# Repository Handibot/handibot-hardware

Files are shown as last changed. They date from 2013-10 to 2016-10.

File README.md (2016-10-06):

handibot-hardware
=================

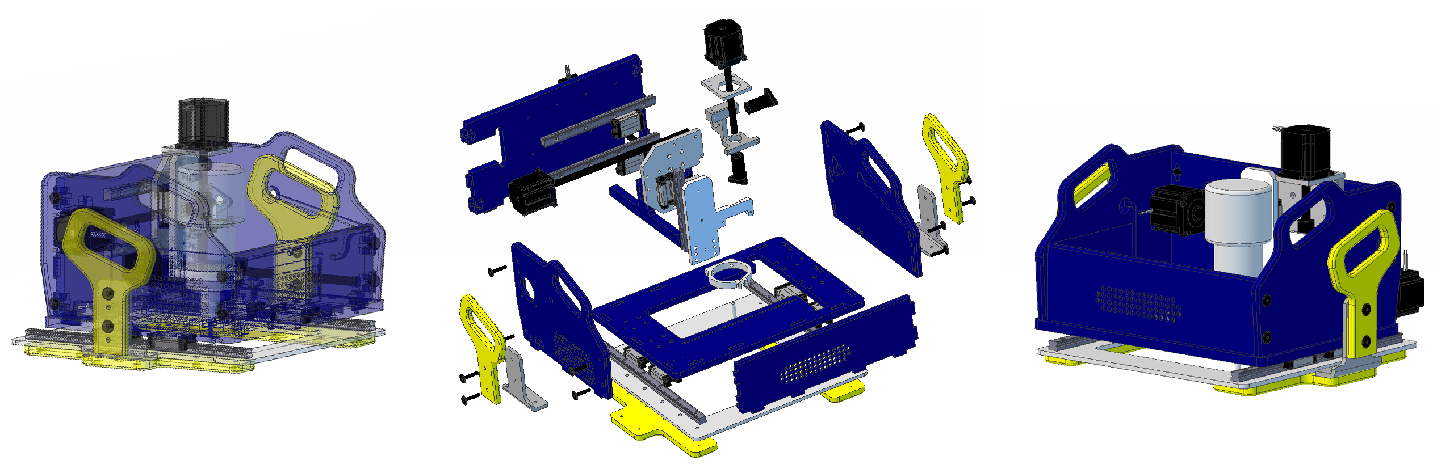
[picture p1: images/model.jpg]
Handibot Assembly


A Handibot tool is a new kind of portable, digitally-controlled power tool for cutting, drilling, carving, and many other machining operations– the first Universal Digital Power Tool (UDPT) – or just, a Smart Tool. If you're familiar with industrial CNC (computer numerically controlled) equipment, think of the Handibot tool as a portable version of CNC. But instead of taking material to a stationary machine, you bring the Handibot to your material -- your jobsite, your remodeling task, your project, your work.

You can put your Handibot tool to work on a table, the floor, the ceiling, the wall, wherever you need to precisely cut, drill, or carve. Armed with a software application developed just for the kind of job you need to do, a Handibot tool is ready to go to work on your job, task, or project with a squeeze of the “Start” button.

Open Source
===========
Handibot is an “open innovation” project. Handibot runs on the open-source, [FabMo digital fabrication platform](https://gofabmo.org). And, to encourage the evolution of hardware and accessories, Handibots are open source hardware (OSH or OSHW). This GitHub repository is the definitive open source hardware documentation for the Handibot system.

The philosophy of this open-source project and our plans for its development can be found on the [Handibot website Open-Innovation pages](https://handibot.com/open-source.php#open_innovation). We recognize that hardware sources and documentation placed on GitHub, while properly archival, can be difficult to view. So as a supplement, we additionally place the definitive STP files as well as additional production files and documents on more exploration-friendly sites which we strive to keep current.

At the moment, Handibot materials can be explored on [GrabCAD](https://workbench.grabcad.com/workbench/projects/gcuAc_g79JwJj5xoyB_sCtAKoUyXaXH0NyeRYptWOwEOWN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). 

For more Handibot Information and our Kickstarter history, see these links:

* [Handibot Website](http://www.handibot.com)
* [Handibot Kickstarter](http://www.kickstarter.com/projects/1320575205/handibottm-a-smart-digital-power-tool?ref=live)

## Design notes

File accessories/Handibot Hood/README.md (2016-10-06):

Handibot Hood
=============

![Handibot Hood]
(https://github.com/Handibot/handibot-hardware/blob/master/accessories/Handibot%20Hood/Handibot_Hood.png)

An eclosure for Handibot v1.0 and v1.1. This "Hood" helps contain dust and debris and reduces router noise. Designed by David Preiss.

* STP Model of parts for full Enclosure (Hood 1.0)

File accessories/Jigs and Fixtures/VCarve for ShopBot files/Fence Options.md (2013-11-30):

# Handibot Fence options #

Two options for a fixed front fence for a Handibot Smart Power Tool. The edge of the fences line up with the Y=0 point of the tool when zeroed with the homing switches, which gives an accurate reference point for cutting.

Two options are shown for a replaceable sacrificial section in the section where cutting happens..a press-fit insert that is cut with the Handibot, and a 1/4"  thick insert that is attached with double-sided carpet tape.

The parts are cut with a 1/4" diameter bit and the file has two layers. The *t-nut pocket* layer contains shallow recesses for the two t-nuts and should be run first. The *cutout* layer drills holes and cuts out the fence.

After the cutting is complete, press or hammer two t-nuts into the recess in the bottom, then flip the fence over and bolt it to the front edge of the Handibot using the two bolt holes in the yellow base.

**NOTE:** *The right-most flange of the clear acrylic base lines up with the right-most bolt hole in the front of the yellow base, and even though the heads of the bolts are low profile there is a chance that the flange may hit the bolt head. If that looks like it's going to happen on your tool, the front edge of that flange can be filed or ground a little to give clearance.*

## Materials ##

- 3/4" plywood, HDPE, mdf, or similar stable sheet goods, at least 20" x 2.5". File is sized for material that is actually .72" thick which seems to most common. Also 1/4" thick material if the thin insert is used, 6.5" long x .72" wide 

- 2 @ 1/4-20 4-prong t-nut... [http://shop.stafast.com/t-nuts/standard/4-prong/142074](http://shop.stafast.com/t-nuts/standard/4-prong/142074) or equivalent

- 2@ 1/4-20 x 25mm decorative bolts... [http://shop.stafast.com/bolts/decorative-head-bolts/17mm-head-no-shoulder/bb142025uhdft](http://shop.stafast.com/bolts/decorative-head-bolts/17mm-head-no-shoulder/bb142025uhdft) or equivalent

- a 4mm or 5/32" Allen wrench

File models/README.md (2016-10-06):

Handibot Base Model (STP) History
=================================
(We have selected STP files to provide the definitive versions of Handibot. Along with PDF BOM's in a separate folder, they consititute the reference design for Handibots and are stored here on GitHub. We will make other types of models, documentation, and production files available as appropriate and convenient. These we will strive to keep updated and available at sites that make exploration convenient.)

* Initial Handibot V 1.00.00 (Publically shown at launch at HIW and Marker Faire, San Mateo, May 2013; earlier prototypes from 7/2012)
* Handibot V 1.01.00 (from 9/10/2013; first Kickstarter Production version)
* Handibot V 1.02.00 (1/13/2014; includes small updates to Kickstarter)
* Handibot V 1.03.00 (3/12/2014; Release Version "Handibot Developer Edition")
* Handibot V 1.10.00 (1/15/2015; Updated "1.1 Developer Edition")
* Handibot V 1.10.07 (9/18/2015; last release of "Developer Edition")

* Handibot V 2.00.00 (3/1/2016; Release Version "Handibot Adventure Edition")

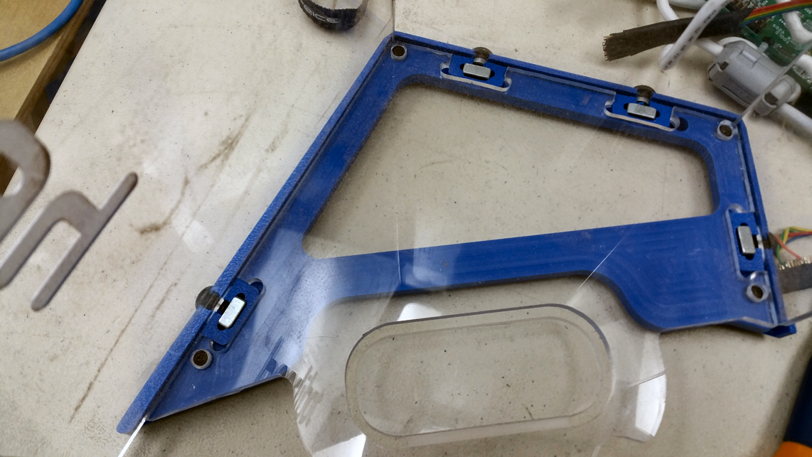
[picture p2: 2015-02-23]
accessories/Handibot Hood/Hood_EndPiece_Inside.png

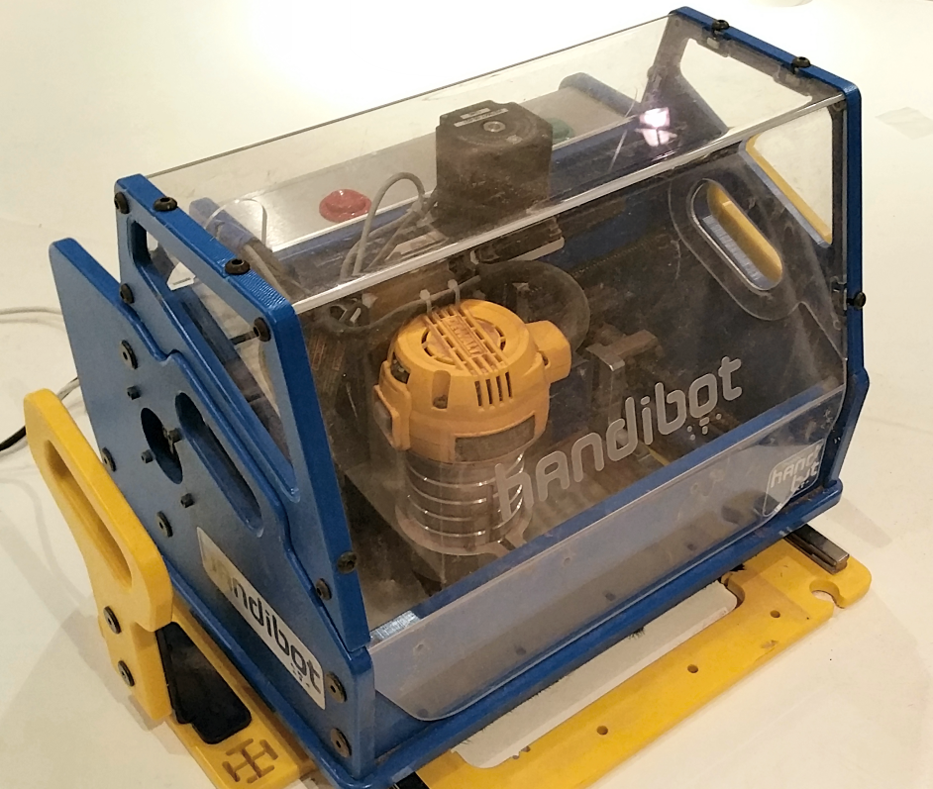
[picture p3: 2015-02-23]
accessories/Handibot Hood/Handibot_Hood.png

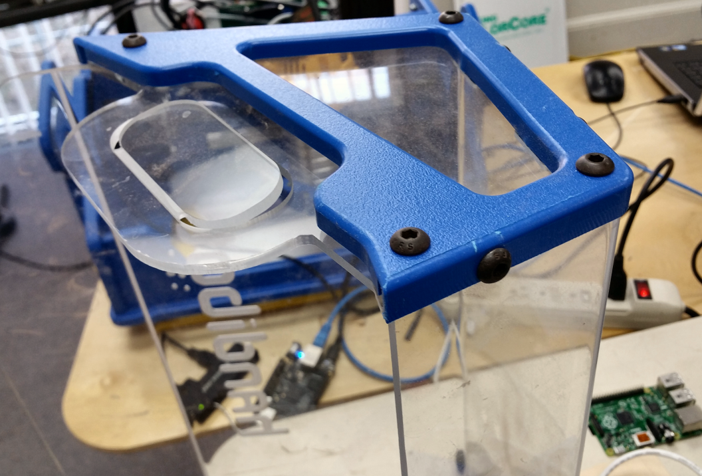
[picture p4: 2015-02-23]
accessories/Handibot Hood/Hood_EndPiece_Outside.png

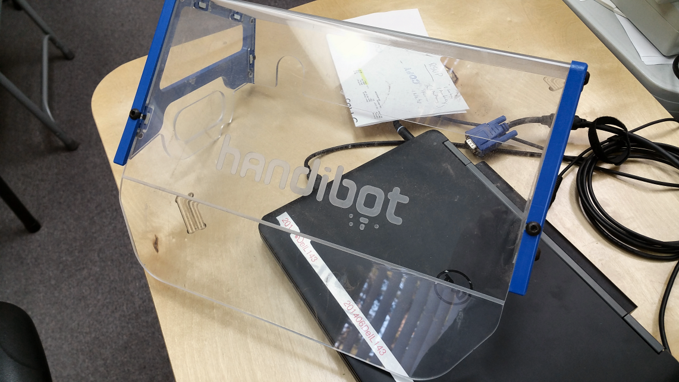
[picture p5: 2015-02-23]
accessories/Handibot Hood/Hood_Acrylic_Front.png

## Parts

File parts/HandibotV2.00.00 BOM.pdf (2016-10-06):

Handibot V2.0

Description | Vendor | Vendor # | SB part # | Qty
Total Sales Price | | | | 1
Assembly Labor | | | | 8
X Gusset | USAD | 4762 | 2
Nut Bracket | USAD | 4761 | 2
Z Plate | USAD | 4652 | 1
Router Bracket Connector | USAD | 4654 | 1
Router Bracket Upper | USAD | 4655 | 1
Router Bracket Lower | USAD | 4656 | 1
Z Motor Plate | USAD | 4657 | 1
X-Z Carriage | USAD | 4659 | 1
X Rail Backing Plate | USAD | 4660 | 1
X Motor Plate | USAD | 4661 | 1
Y Bearing Backing Plate | USAD | 4662 | 2
Y Nut Holder | USAD | 004894 | 1
Cable Guide Tray | USAD | 4663 | 1
Cable Guide Barrier | USAD | 4664 | 1
Z Zero Plate | USAD | 4665 | 1
Y Motor Plate | USAD | 4666 | 1
Base Plate Backing | USAD | 4667 | 1
Y Nut Bracket | USAD | 4668 | 1
Bracket Universal Mount | USAD | 3653 | 2
Handibot Machined Parts Kit | USAD | 4764 | 1
Hood Face | Handibot | 4669 | 1
Hood Side Window | Handibot | 4670 | 2
Electronics Enclosure | Handibot | 4671 | 1
LED Strip Cover | Handibot | 4672 | 1
Tool Holder Window | Handibot | 4673 | 1
Rear Neoprene Plate | Handibot | 4674 | 1
Front Neoprene Plate | Handibot | 4675 | 1
Side Neoprene Plate | Handibot | 4676 | 1
Rear Neoprene | Handibot | 4677 | 1
Front Neoprene | Handibot | 4678 | 1
Side Neoprene | Handibot | 4679 | 1
Logo Plate | Handibot | 4680 | 2
Base Plate HDPE | Handibot | 4681 | 1
Button Holder HDPE | Handibot | 4682 | 1
Electronics Partition HDPE | Handibot | 4683 | 1
Electronics Wall HDPE | Handibot | 4684 | 1
Tool Holder Frame HDPE | Handibot | 4685 | 1
Vacuum Foot HDPE | Handibot | 4686 | 1
Rear Wall HDPE | Handibot | 4687 | 1

## Bill of Materials

Hood Left Side HDPE | Handibot | | 4688 | 1
Hood Right Side HDPE | Handibot | | 4689 | 1
Tie Plate HDPE | Handibot | | 4690 | 1
Y Motor Holder HDPE | Handibot | | 4691 | 1
Mid Plate HDPE | Handibot | | 4692 | 1
Y Motor Guard HDPE | Handibot | | 4693 | 1
ExoFrame Base HDPE | Handibot | | 4694 | 1
Sensor Holder HDPE | Handibot | | 4695 | 0
ExoFrame Left Side HDPE | Handibot | | 4696 | 1
ExoFrame Right Side HDPE | Handibot | | 4697 | 1
Handle HDPE | Handibot | | 4704 | 1
Handibot Cut Parts Kit | Handibot | | 4765 | 1
Motor Actuator X 315mm | Haydon Kerk | K57M4Y-05-019 | 3621 | 1
Motor Actuator Y 270mm | Haydon Kerk | K57M4Y-05-020 | 3622 | 1
Motor Actuator Z 150mm | Haydon Kerk | K57M4Y-05-021 | 3623 | 1
Block Linear Rail | Accu-Tech | SME 15SBSSFC | 3864 | 7
Assembly Rail Linear 242 | Accu-Tech | SME 15 SB 1 SS +R242-31/31N | 4093 | 2
Rail Linear 366 | Accu-Tech | SME 15 SB 2 SS +T366 -33/33N | 4076 | 2
Assembly Rail Linear 168 | Accu-Tech | SME 15 SB 1 SS +R168 -24/24N | 4095 | 1
Micro Step Drive G250X | Gecko Drive | G250X | 2780 | 4
Assy Interface Handibot | GRT | HB-5 | 4544 | 1
Fabmo Card | | | 4629 | 1
Power Supply | Emco | HRP-150-24 | 3664 | 1
Switch Stop | Spark Fun | COM-09336 | 3662 | 1
Switch Go | Spark Fun | COM-09341 | 3663 | 1
Cord Power | Jameco | 2099999 | 3711 | 1
Guard Fan | Jameco | 1952708 | 3713 | 1
Board Arduino | Spark Fun | DEV-11113 | 3697 | 1
Lights Indicator LED | AdaFruit | 001138 | 3698 | 0.16
Thermal Pad 0.10x8x16 | Digikey | 926-1114-ND | 3118 | 0.166
WAGO right angle | EMCO | | | 1
Connector Wago 2 Pin Male | EMCO | 231-602 | 163 | 1
WAGO Board Connector | EMCO | | 004177 | 2
Switch Rocker W/V Lock | Digikey | 486-1638-ND | 3834 | 1
Cable 18 2C Unshielded | Machine Controls | 450003-15 | 4705 | 52
Cable 4C 18 AWG STR BC | ANIXTER | 8489 | 95 | 34
Cable 2Cx0.25 Br & W | Machine Controls | 117039 | 3004 | 12
Black 18 AWG | Digikey | C2064B-1000-ND | 4600 | 20
White 18 AWG | Digikey | C2064W-1000-ND | 159 | 19
Blue 18 AWG | Digikey | C2064L-1000-ND | 4838 | 14
Green 18 AWG | Digikey | C2064G-1000-ND | 4601 | 5
Ribbon Cable | Jameco | 643559 | 864 | 6
USB Short cable | | | | 1
Heat Shrink 2"x40mm Black | Heat Shrink | B2(3x)x40mm | 1648 | 1.5
22-16 AWG Female Disconnect | Jameco | 489627 | 3796 | 8
Grey Ferrule | Fastenal | 0749603 | 3419 | 2

White Ferrule | Fastenal | 0749600 | 3505 | 4
Red Ferrule | Fastenal | 0749607 | 3777 | 1
18-22 AWG Female Terminal | Jameco | 489643 | 3795 | 4
Z Zero Clip | Digikey | 314-1084-ND | 4790 | 1
Relay 24V | Digikey | PB1008-ND | 3699 | 1
Connector Fork 22-16 AWG | Fastenal | 0720185 | 2758 | 11
Zip Tie Anchor | McMaster | 7566K29 | 4821 | 3
Cable Tie 6" Black | Fastenal | 63124 | 3108 | 13
M3x16 BHSCS | McMaster | 92095A184 | 5079 | 2
M4x10 SHCS | Fastenal | 39524 | 3053 | 10
M4x16 SHCS | McMaster | 90128A215 | 4818 | 14
M4x20 SHCS | Fastenal | 11103313 | 3096 | 6
M4x14 BHSCS | Fastenal | 39901 | 4748 | 17
M4x16 BHSCS | Fastenal | 39902 | 4749 | 19
M4x20 BHSCS | Fastenal | 39903 | 4750 | 1
M4 x 10 FHSCS | McMaster | 91294A190 | 4822 | 2
M4 x 10 Nylon Screw | McMaster | 92492A220 | 4816 | 2
M5 x 20 SHCS | Fastenal | | 3873 | 2
M5x10 BHSCS | Fastenal | MB2540010A2000 | 4751 | 8
M5x14 BHSCS | Fastenal | 11510097 | 3810 | 12
M5x20 FHSCS | Fastenal | 1139947 | 4753 | 4
M6x18 FHSCS | Fastenal | 40947 | 4755 | 5
2-56x1/4 SHCS | Fastenal | 73399 | 4743 | 8
6-32 x 5/16 BHSCS | Fastenal | 73763 | 4744 | 8
6-32 x 5/8 Standoff | Fastenal | 146059 | 4759 | 4
1/4-20 x 1/2 BHSCS | Fastenal | 24049 | 2134 | 11
1/4-20 x 3/4 BHSCS | Fastenal | 24051 | 2135 | 1
1/4-20 x 1 BHSCS | Fastenal | 140675 | 3802 | 7
1/4-20 x 7/16 FHSCS | McMaster | 92210A536 | 4817 | 1
1/4-20 x 20mm Connector Bolt | Fastenal | 140675 | 3802 | 4
1/4-20 x 30mm Connector Bolt | Fastenal | 140679 | 3667 | 37
1/4-20 Square Nut | Fastenal | 37619 | 4419 | 48
#6 x 3/8 FH Sheet Metal Screw | Fastenal | 31528 | 4756 | 6

#6x1/2 PPH | Fastenal | 1131226 | 4423 | 2

#8 x 3/8 PPH | Fastenal | 0143200 | 4422 | 8

#8 x 3/8 FH Sheet Metal Screw | Fastenal | 148505 | 4757 | 25

#8x1/2 Pan Head | Fastenal | 0143318 | 4421 | 2

#10 x 1/2 Pan Head | Fastenal | 31341 | 4758 | 9

1/4x1/4x#8 Aluminum Spacer | Fastenal | 146031 | 4760 | 2
Plastic Countersunk Washer | McMaster | 95481A035 | 4819 | 1
0.375 x 0.25 Magnet | Apex Mag | M38x14DI | 4815 | 4
Vacuum Tube | McMaster | 5500K31 | 4789 | 1.2
Brush 120"x1.6" Exposed | Sealeze | FXD80IH16BL | 3376 | 12.5
Extension Spring | McMaster
3/8 x 0.012 Spring Steel Banding | McMaster | 9075K46 | 4820 | 13
3mm T Handle Allen | McMaster | | 005080 | 1

4mm T Handle Allen | McMaster | 4787

1
2mm Allen L key | | | 005081 | 1
Pointer | Handibot | | 4788
User Manual | Handibot | | 4786 | 1
vCarve Pro | Vectric | | 11149
ShopBot Control License | ShopBot | | 11161 | 1
Dewalt Router | Dewalt | | 12012
Foam Back Packaging | Handibot | | 4768 | 2
Foam Bottom Packaging | Handibot | | 4769
Foam Top Packaging | Handibot | | 4770 | 1
Foam Front Packaging | Handibot | | 4771
Test Board | Handibot | | | 1
Box 22 x 18 x 16 | Uline | S-16458 | 4767

1

1

1

1

1

1

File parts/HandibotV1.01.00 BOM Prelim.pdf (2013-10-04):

Part # | PART NAME | REQUIRED
003646-01 | Exoframe Side Right HDPE | 1
003647-01 | Exoframe Side Left HDPE | 1
003648-01 | Exoframe Front HDPE | 1
003649-01 | Exoframe Rear HDPE | 1
003650-01 | Exoframe Bottom HDPE | 1
003674-01 | Pad Base HDPE | 1
003652-01 | Handle Outboard HDPE | 2
003653-01 | Bracket Universal Mount | 2
| Cover Fairing Acrylic
| Linear Motion
003621-01 | Motor Actuator X 315mm | 1
003622-01 | Motor Actuator Y 270mm | 1
003623-01 | Motor Actuaror Z 150mm | 1
with motor | Nut Antibacklash X | 1
with motor | Nut Antibacklash Y | 1
with motor | Nut Antibacklash Z | 1
003655-01 | Carrier Antibacklash nut Y HDPE | 1
002876-01 | Carrier Antibacklash nut Z&X Aluminum | 2
003656-01 | Rail Anti Backlash Nut Carrier Y HDPE | 1
004002-01 | Rail Linear X 235mm | 2
004003-01 | Rail Linear Y 360mm | 2
004004-01 | Rail Linear Z 162mm | 1
004001-01 | Bearing Linear Rail X,Y,Z | 7

Carriage
003657-01 | Plate Carriage | 1
003658-01 | Plate Z | 1
003659-01 | Plate Motor Z | 1

003660-01 | Bracket Router | 1
003661-01 | Gusset Z Plate | 1
| Electronics
002780-01 | Driver Gecko X,Y,Z | 3
003118-01 | Thermal Pad heatsink plate | 1
003591-01 | Board Interface | 1
003601-01 | Card Controller | 1
003662-01 | Switch Stop | 1
003663-01 | Switch Go | 1
| Board Arduino | 1
| Lights Indicator LED | 1
003664-01 | Power Supply 24V 150W | 1
| Contactor 24V | 1
003665-01 | Switch Rocker | 1

Wire
Crimp connectors
Heat shrink

Hardware
T-nut dropin | 27
Bolt 1/4" x30mm | 27
Standoff Interface board | 4
SHCS M4x12 | 32
SHCS M4x16 | 15
SHCS M4x20 | 4
BHCS M5x20 | 2
SHCS M6x20 | 28
Nut nylock M4 | 8
BHCS M4x40 | 3
SHCS M4x70 | 4
bolts for standoffs/heatsink plate | 8
SHCS #2-56 | 6
Router Dewalt | 1

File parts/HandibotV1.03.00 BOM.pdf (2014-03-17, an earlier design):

Vendor Part # | SB Part # | Vendor of Record | Category | QTY. REQ
| | | Mechanical
| 003651 | Norva Plastics | HDPE BLUE 4x10x.5 (Compression Polymers) | 0.2500
| 003677 | Norva Plastics | HDPE YELLOW 4x10x.5 (Compression Polymers) | 0.08
003646 | 003646 | Norva Plastics/Shopbot | Exoframe Side Right HDPE | 1
003647 | 003647 | Norva Plastics/Shopbot | Exoframe Side Left HDPE | 1
003648 | 003648 | Norva Plastics/Shopbot | Exoframe Front HDPE | 1
003649 | 003649 | Norva Plastics/Shopbot | Exoframe Mid HDPE | 1
003650 | 003650 | Norva Plastics/Shopbot | Exoframe Bottom HDPE | 1
003674 | 003674 | Norva Plastics/Shopbot | Baseplate | 1
003652 | 003652 | Norva Plastics/Shopbot | Handle Outboard HDPE | 2
003676 | 003676 | Norva Plastics/Shopbot | Exoframe Lid Partition HDPE | 1
003675 | 003675 | Norva Plastics/Shopbot | Exoframe Partition Rt HDPE | 1
003671 | 003671 | Norva Plastics/Shopbot | Exoframe Partition Lt HDPE | 1
003670 | 003670 | Norva Plastics/Shopbot | Exoframe Rear HDPE | 1
003653 | 003653 | Norva Plastics/Shopbot | Bracket Universal Mount | 2
80664 | 003696 | Century Spring | Spring Z Assit | 1
| 003710 | Raleigh Rubber and Gasket | Neoprene 4x8x.0625" with Pressure sensitive adhesive applied | 0.0556
003703 | 003703 | Raleigh Rubber and Gasket/Shopbot | Pad Baseplate Neoprene | 1
003865 K57M4Y-05-019 | 003865 | Norva Plastics/Shopbot | Baseplate Pointer | 1
| | | Linear Motion
| 003621 | Haydon Kerk | Motor Actuator X 315mm | 1
K57M4Y-05-020 | 003622 | Haydon Kerk | Motor Actuator Y 270mm | 1
K57M4Y-05-021 | 003623 | Haydon Kerk | Motor Actuaror Z 150mm | 1
002876 | 002876 | USA Dutch | Nut Block Upper | 2
003655 | 003655 | USA Dutch | Carrier Antibacklash nut Y Aluminum | 1
003656 | 003656 | USA Dutch | Rail Anti Backlash Nut Carrier Y HDPE | 1
MSB 15 SS FCN | 004001 | Accu-Tech USA | Block | 7
MSB 15 T235-27.5/27.5 N | 004002 | Accu-Tech USA | Rail Linear X 235mm | 2
MSB 15 T360-30/30 N | 004003 | Accu-Tech USA | Rail Linear Y 350mm | 2
MSB 15 U162-21/21 N | 004004 | Accu-Tech USA | Rail Linear Z 162mm | 1
| | | Carriage
003311 | 003311 | USA Dutch | Mount Spring DT Z | 1
003657 | 003657 | USA Dutch | Plate Carriage | 1
003658 | 003658 | USA Dutch | Plate Z | 1
003659 | 003659 | USA Dutch | Plate Motor Z | 1
003660 | 003660 | USA Dutch | Bracket Router | 1
003661 | 003661 | USA Dutch | Gusset Z Plate | 1
003672 | | | Electronics
| 003672 | USA Dutch | Enclosure Electronics | 1
G250X | 002780 | Gecko Drive | MICRO STEP DRIVE G250X | 3
926-1114-ND | | Digikey | Thermal Pad .010" x 8" x 16" | 0.14
| 003118 | DigiKey/Shopbot | Thermal Pad heatsink plate | 1
| 003786 | GRT | Assy Interface Handibot | 1
| 003601 | PSI | Card Controller V211 | 1
USBPNLBFBM1 | 003685 | StarTech | Cable USB Panel Mount B to B - F/M 1 ft | 1
USBPRT | 002190 | Dramen | CABLE USB A/B | 1
COM-09336 | 003662 | Spark Fun | Switch Stop | 1
COM-09341 | 003663 | Spark Fun | Switch Go | 1
2099999 | 003711 | Jameco | Cord Power | 1

56P2967 | 003712 | Newark | Filter Fan Media | 1
1952708 | 003713 | Jameco | Guard Fan | 1
7378K225 | 003714 | McMaster-Carr | Loom Wire | 0.05
RP465-ND | 000102 | DigiKey | Cordgrip Power | 1
DEV-11113 | 003697 | Spark Fun | Board Arduino | 1
001138 | 003698 | AdaFruit | Lights Indicator LED | 0.16
HRP-150-24 | 003664 | Emco | Power Supply 24V 150W | 1
PB1008-ND | 003699 | DigiKey | Relay 24V | 1
WM2011-ND | 003128 | DigiKey | CONN HOUSING 2POS .100 W/RAMP | 3
WM1114CT-ND | 003129 | DigiKey | CONN TERM FEMALE 22-30AWG TIN | 6
CKN9956CT-ND | 003013 | DigiKey | SWITCH DETECT MICRO SPST SMD | 3
WM4200-ND | 003131 | DigiKey | CONN HEADER 2POS .100 VERT TIN | 3
473-1005-ND | 003132 | DigiKey | PCB COPPERCLAD 12X12 1/16" 1SIDE | 0.02
003700 | 003700 | ShopBot | Switch Proximity X | 1
003701 | 003701 | ShopBot | Switch Proximity Y | 1
003702 | 003702 | ShopBot | Switch Proximity Z | 1
1091-1162-ND | 003665 | DigiKey | Switch Rocker | 1
| | | Wire 18 AWG Black 20" | 0.00167
| | | Wire 18 AWG White 30" | 0.0025
410002-06 | 003694 | Machine Control | Wire 18 AWG Blue 30" | 0.0025
117039 | 003004 | Machine Control | Cable 2Cx0.25 Br & W 78" | 0.013
2003A | 001664 | Emco | Cable 3C BK R G 80 Deg. 300v 19" | 0.0016
643559 | 000864 | Jameco | Cable Ribbon 16C 6" | 0.005
117050 | 003008 | Machine Control | Cable DT MTR 4x0.34 31" | 0.00258
489643 | 003795 | Jameco | Quick Disconnect Terminal 18-22 AWG Female 19.81mm 8.02mm | 4
489627 | 003796 | Jameco | Quick Disconnect Terminal 18-22 AWG Female 21.84mm 9.65mm | 6
749600 | 003505 | Fastenal | 22 AWG 0.31"/7.8mm Strip Power Phase[REG] Wht Nylon Insulated Ferrule End Sleeve | 14
749603 | 003419 | Fastenal | 20 AWG 0.30"/7.5mm Strip Power Phase[REG] Gray Nylon Insulated Ferrule End Sleeve | 1
WM2901-ND | 003797 | DigiKey | Conn Housing 3 Pos Female .100 W/LATCH | 1
WM2513-ND | 003798 | DigiKey | Conn Term Female 24-30AWG GOLD | 3
WM2534-ND | 003799 | DigiKey | Conn Housing 3 Pos Male .100 | 1
WM2563CT-ND | 003800 | DigiKey | Conn Pin Male 24-30AWG CRIMP 15GOLD | 3
70078437 | 003801 | ALLIED | Ferrule, Dual Wire; 18 AWG; 2; HH 2 x 1.0/15; Red; 0.43 in.; 0.61 in.; 0.32 in. | 1
ASC16H-ND 961746 | 001535 | DigiKey | CONN IDC SOCKET 16POS | 2
| | | Hardware
| 003666 | Fastenal | T-nut dropin | 29
140679 | 003667 | Fastenal | Bolt Connector 1/4-20 x30mm | 29
140675 | 003802 | Fastenal | Bolt Connector 1/4-20 x20mm | 4
92492A128 | 003803 | McMaster-Carr | MS PPH M3x20 Nylon Black | 6
93369A116 | 003804 | McMaster-Carr | Nut hex Nylon Black | 6
1123201 | 001601 | Fastenal | SHCS 1/4-20 x 1/2 | 4
145924 | 003805 | Fastenal | Standoff 6-32 nylon | 4
1139524 | 003053 | Fastenal | SHCS M4x10 | 4
1139525 | 002910 | Fastenal | SHCS M4x12 | 41
1139518 | 003806 | Fastenal | SHCS M4x14 | 18
1139526 | 003396 | Fastenal | SHCS M4x16 | 5
1139527 | 003054 | Fastenal | SHCS M4x20 | 6
039536 | 003807 | Fastenal | SHCS M4x80 | 4
1139529 | 003668 | Fastenal | BHCS M4x30 | 2
1139545 | 003808 | Fastenal | SHCS M5x12 | 1

040878 | 003810 | Fastenal | BHCS M5x14 | 10
040879 | 003809 | Fastenal | BHCS M5x16 | 30
1140147 | 003562 | Fastenal | Nut hex nylock M4 | 12
1128795 | 003811 | Fastenal | MS PPH 6-32 x 3/8 | 4
90259A218 | 003812 | McMaster-Carr | Threaded insert M5 | 2
023024 | 002920 | Fastenal | SHCS #2-56 | 6
1139584 003746 | 003813 | Fastenal | SHCS M8-1.25x10 | 1
| | | Dust Collector | 1
| 003746 | Norva Plastics/Shopbot | Channel Dust Collector Front | 1
003747 | 003747 | Norva Plastics/Shopbot | Channel Dust Collector Rear | 1
24111102 | 003814 | Sabic | Acryllic 4'x8'x0.118" Duraplex 70% | 0.0357
003748 | 003748 | Sabic/Shopbot | Cover Plate Dust Collector | 1
21014102 | 003815 | Sabic | Acryllic 4'x8'x0.060" Optix | 0.003
003749 | 003749 | Sabic/Shopbot | Cover Plate LED | 1
8486K331 | 003751 | McMaster-Carr | Tube Dust Collector 5" | 0.083
FXC80IH10BL | 002972 | Sealeze | Brush Bulk | 0.2
003754 | 003754 | Sealeze/USA Dutch | Brush Dust Collector Front | 1
| | | | 1
003755 | 003755 | Sealeze/USA Dutch | Brush Dust Collector Rear
DWP611 | 12012 | Black & Decker | DEWALT 1.25HP ROUTER
| | | 1
PLA0101178263 | 003010 | Sabic | Acrylic Clear 0.177x51x100 50% | 0.037
003753 | 003753 | Sabic/Shopbot | Deflector Front | 1
37-61 | 13732 | LMT Onsrud | Bit 1/2" 90 degree V bit | 1
52-287 | 10477 | LMT Onsrud | Bit 1/4" 2 Flute Upcut | 1
61-040 | 13728 | LMT Onsrud | Bit 1/8" Single Flute | 1
| 11160 | Vectric | Software V Carve pro, Cut 3D | 1
011161 | 11161 | ShopBot | Software Control Software License | 1
| 003735 | Rand Whitney | Box Shipping Handibot | 1

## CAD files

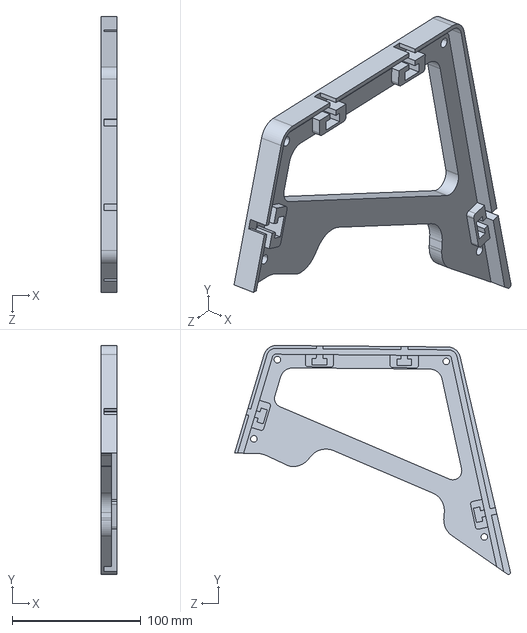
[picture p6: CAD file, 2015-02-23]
accessories/Handibot Hood/Full Enclosure HDPE Slotted Sides.STEP
12.7 x 177.8 x 214.2 mm

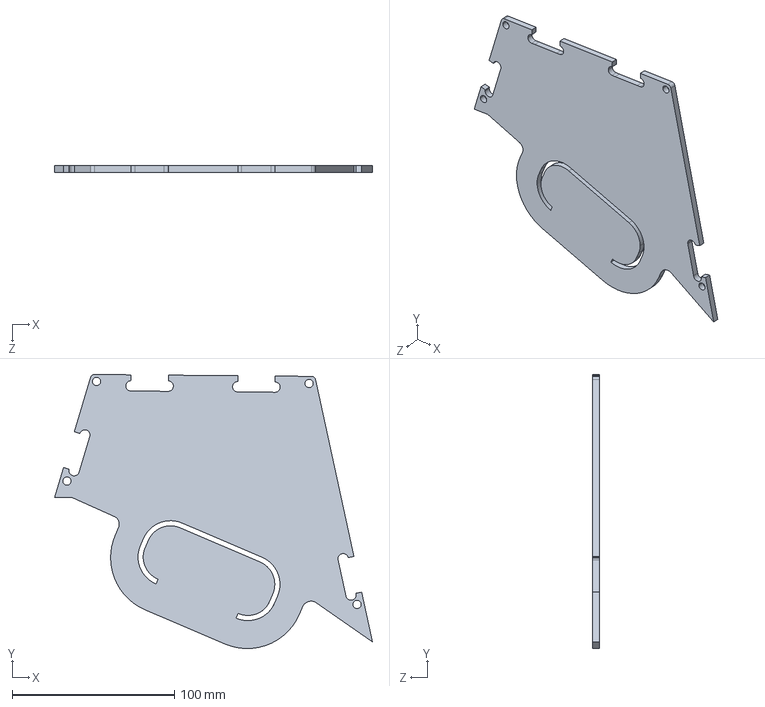
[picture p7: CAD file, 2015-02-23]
accessories/Handibot Hood/Full Enclosure Acrylic Slotted Slides_NoRelief.STEP
196.1 x 169.0 x 4.32 mm

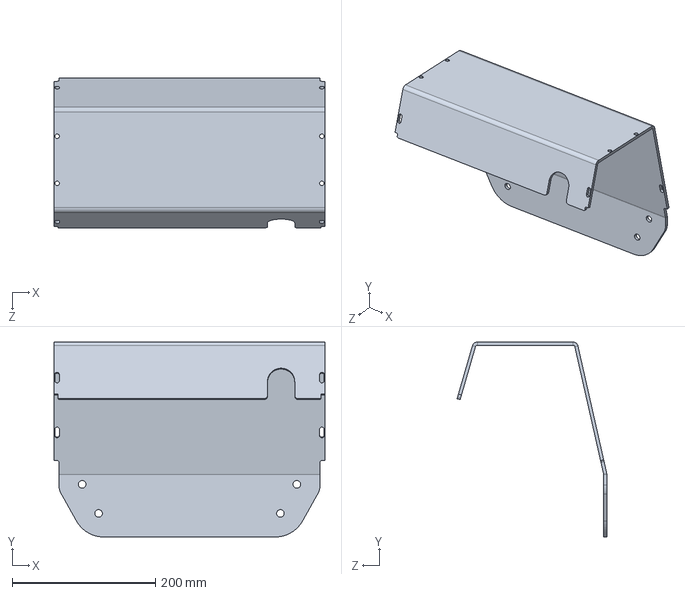
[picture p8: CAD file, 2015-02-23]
accessories/Handibot Hood/Full Enclosure Flat Pattern.STEP
379.0 x 272.7 x 209.6 mm

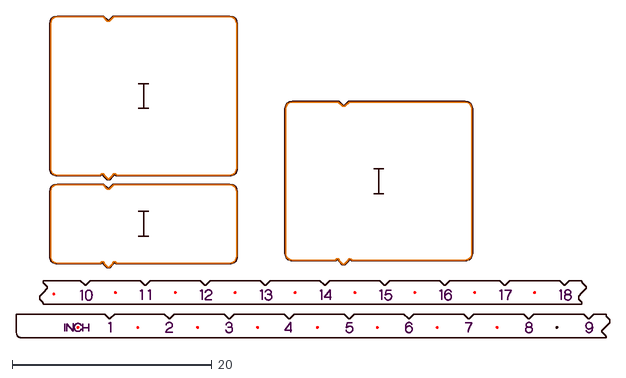
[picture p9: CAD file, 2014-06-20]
accessories/Jigs and Fixtures/DXF files/handibot large material sheet jig v2.dxf
59.4 x 32.2

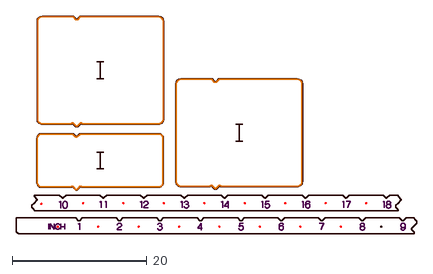
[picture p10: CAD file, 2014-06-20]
Accessories/Jigs and Fixtures/DXF files/Handibot large material indexing jig v2 Inch.dxf
59.4 x 32.2

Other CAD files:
accessories/Handibot Hood/Full Enclosure Flat Pattern.DXF
accessories/Handibot_cut/Index Blocks/Sketchup/Index Blocks.skp
accessories/Jigs and Fixtures/Sketchup Models/Handibot base for small part holding.skp
accessories/Jigs and Fixtures/Sketchup Models/Handibot fence options.skp
accessories/Jigs and Fixtures/Sketchup Models/Handibot wall jig.skp
accessories/Jigs and Fixtures/Sketchup Models/Handibot wavy indexing jig.skp

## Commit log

2013-10-04 Prelim BOM V1.01.00 posted
2013-11-27 updated jig files
    [Handibot base for small part holding.skp, Handibot fence options.skp, Handibot wall jig.skp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]
2013-11-27 housekeeping and adding back fence options
    [Handibot base for small part holding.skp, Handibot fence options.skp, Handibot wall jig.skp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]
2013-12-02 Added Gauge Blocks
    [Guage Blocks.skp]
2014-06-20 Added Large material indexing jig set v2
    Added the jig parts for the v2 large material jig set from Handibot
    store. Reorganized the Jigs and Fixtures folder
    [Handibot base for small part holding.skp, Handibot fence options.skp, Handibot large material indexing jig v2 Inch.dxf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]
2014-06-20 Fixed sync collision
    [Handibot base for small part holding.skp, Handibot fence options.skp, Handibot large material indexing jig v2 Inch.dxf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]
2014-06-20 Revert "Fixed sync collision"
    This reverts commit 8abe31999bf7c5534f9465a729a087ae4e1c2746.
    [Handibot base for small part holding.skp, Handibot fence options.skp, Handibot large material indexing jig v2 Inch.dxf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]
2014-06-20 Revert "Added Large material indexing jig set v2"
    This reverts commit 2ec91cd5a3275d3e16fae0595be001716298e671.
    [Handibot base for small part holding.skp, Handibot fence options.skp, Handibot large material indexing jig v2 Inch.dxf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]
2014-06-20 Added Indexing jig parts from Handibot store
    Added v2 indexing jig parts in VCarve crv format, dxf, and svg
    [handibot large material sheet jig v2.dxf]
2015-02-23 load STPs for Hood
    [Full Enclosure Acrylic Slotted Slides no relief.STEP, Full Enclosure Flat Pattern.DXF, Full Enclosure Flat Pattern.STEP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]
2015-09-21 Stage 1 of 2-stage rename
    [Full Enclosure Acrylic Slotted Slides no relief.STEP, Full Enclosure Flat Pattern.DXF, Full Enclosure Flat Pattern.STEP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]
2015-09-21 Stage 2
    [Full Enclosure Acrylic Slotted Slides no relief.STEP, Full Enclosure Flat Pattern.DXF, Full Enclosure Flat Pattern.STEP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]
2015-09-21 Stage 3 (woops)
    [Full Enclosure Acrylic Slotted Slides no relief.STEP, Full Enclosure Flat Pattern.DXF, Full Enclosure Flat Pattern.STEP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]
2016-10-06 Update files
    [Full Enclosure Acrylic Slotted Slides_NoRelief.STEP]
2016-10-06 Updated BOM
